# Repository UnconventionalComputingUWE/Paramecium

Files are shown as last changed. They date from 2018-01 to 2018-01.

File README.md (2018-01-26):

# Paramecium
Contained in this github are files to create and test artificial cilia.

%%%% Board manufacture %%%%
The eagle files are included in the github so that users may produce articifial cilia. There is a free version of EagleCAD for all users which allows for the modification and design of 2 layered boards, so anyone can edit the files. Some board manufacturers accept EagleCad files however some companies only accept Gerber files; there is a simple method of converting EagleCAD designs to Gerbers in the software.

%%%% Assembling the boards %%%%
The parts can be assembled on the boards by the user or by the board manufacturer should they have such capabilities. Some components are through-hole and some are surface-mount; both can be soldered by hand by anyone with reasonable soldering proficiency.

%%%% Uploading files to the board %%%%
You must upload the hex files (both the supplied one, and user created ones) using an ISP.
We used AVRDUDE to upload hex files via a USBtinyISP AVR Programmer Kit (USB SpokePOV Dongle) - v2.0. Other ISP devices may work.

Anyone is free to use and modify these designs and code for their use. Please provide appropriate credit, such as citations. Commercial use is permitted.

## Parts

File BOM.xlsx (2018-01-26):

 | Bill of Material
Part Name | Part | Mfr. Part. No | number (per board)
COLORSENS (Connectors) | HARWIN M20 Series Crimp Contact, Female, 30AWG to 22AWG, Gold, Tin Plating | M20-1180042 | 4
COLORSENS (Housing) | HARWIN M20-10, 2.54mm Pitch, 4 Way, 1 Row Female Straight Connector Housing | M20-1060400 | 1
U1 (socket) | 3M 4800 2.54mm Pitch Straight 28 Way, Through Hole Stamped pin Open Frame IC Dip Socket, 1A | 4828-3004-CP | 1
U1 | Microchip Technology ATMEGA328P-PU, 8bit AVR Microcontroller, 20MHz, 32 kB Flash, 28-Pin PDIP | ATMEGA328P-PU | 1
ISP | HARWIN M20, 2.54mm Pitch, 6 Way, 2 Row Unshrouded, Straight Pin Header, Through Hole, Solder Termination | M20-9980346 | 1
J1 | RS Pro 2.5mm PCB Mount DC Power Socket 1A | 448-376 | 1
 | Hex Socket Button Steel Black, Self-Colour Socket Screw, M3 x 5mm | Q107380000300005000 | 3
 | HTSB-M3-15-5-1, 15mm High Brass Threaded Hex Spacer 5mm Wide for M3 Thread | HTSB-M3-15-5-1 | 3
C3,C4 | KEMET 22pF Multilayer Ceramic Capacitor MLCC 50V dc ±5% C0G Dielectric 1206 (3216M), Max. Temp. +125°C | C1206C220J5GACTU | 2
 | HTSN-M3-20-6-2, 20mm High Nylon Threaded Hex Spacer 6mm Wide with 8mm Bolt Length for M3 Thread | HTSN-M3-20-6-2 | 3 (optional)
IC2 | Taiwan Semiconductor TS2937CP33 ROG, LDO Regulator, 500mA, 3.3 V, ±2%, -18 → 26 Vin 3-Pin DPAK | TS2937CP33 ROG | 1
Q2 | Crystal 16MHz, ±20ppm, 2-Pin HC-49/U-S SMD | QCS16.0000F18B23M | 1
C1,C2,C5,C6 | Nichicon Aluminium Electrolytic Capacitor 47μF 25V dc 6.3mm Surface Mount CD Series +105°C | UCD1E470MCL1GS | 4
IC1 | ON Semiconductor MC78M05CDTG Linear Voltage Regulator, 700mA, 5 V 3-Pin, D-PAK | MC78M05CDTG | 1
SV1,SV2,SV3,SV4 (Board connector, male) | HARWIN M20, 2.54mm Pitch, 5 Way, 1 Row Unshrouded, Straight Pin Header, Through Hole, Solder Termination | M20-9990546 | 3
S1 | 1 Way Surface Mount DIP Switch SPST, Raised Actuator Slide Actuator | IKD0103101 | 1
SV1,SV2,SV3 (Servo) | Tower Pro SG-50 Micro Digital Servo | SG50 | 3
COLORSENS | Adafruit RGB Sensor | TCS34725 | 1

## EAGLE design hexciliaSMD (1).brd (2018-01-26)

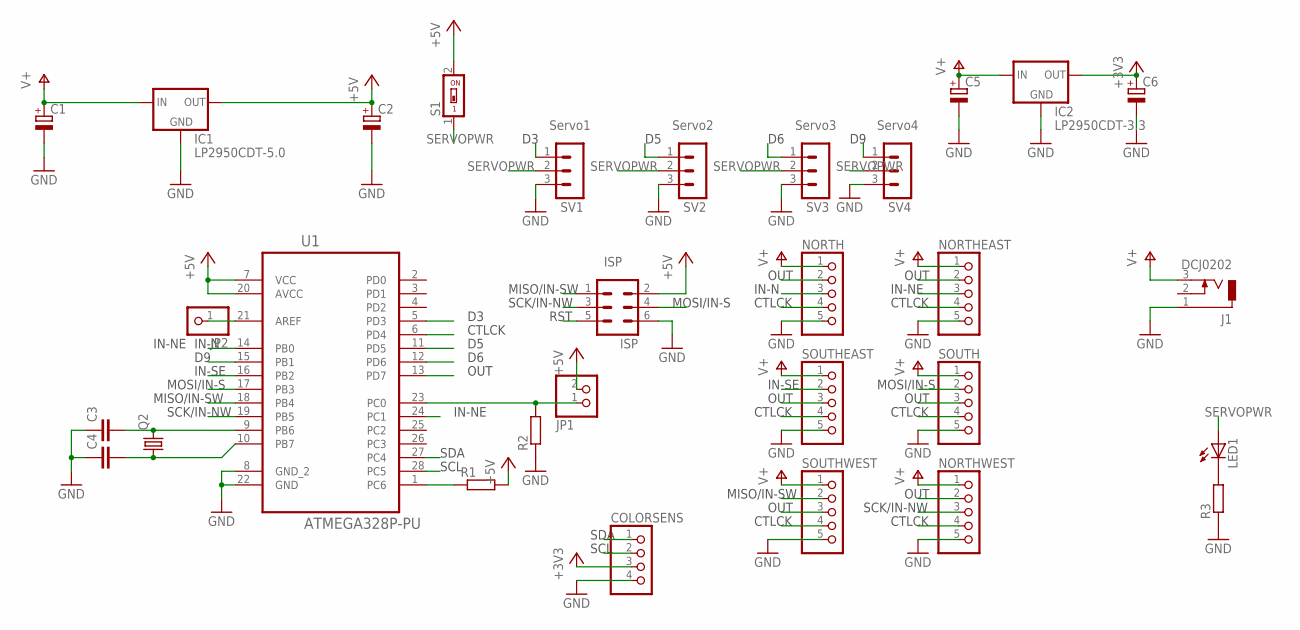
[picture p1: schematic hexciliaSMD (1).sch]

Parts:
C1, C2, C5, C6: CPOL-EU153CLV-0605; 153CLV-0605
C3, C4: C-EUC1210; C1210
COLORSENS: PINHD-1X4; 1X04
IC1: LP2950CDT-5.0; DPACK
IC2: LP2950CDT-3.3; DPACK
ISP: MA03-2
J1: DCJ0202
JP1: PINHD-1X2; 1X02
JP2: PINHD-1X1; 1X01
LED1: LEDCHIP-LED0805; CHIP-LED0805
NORTH: PINHD-1X5; 1X05
NORTHEAST: PINHD-1X5; 1X05
NORTHWEST: PINHD-1X5; 1X05
Q2: CRYSTALHC49UP; HC49UP
R1, R2, R3: R-EU_M1206; M1206
S1: SWS001; SMS-001
SOUTH: PINHD-1X5; 1X05
SOUTHEAST: PINHD-1X5; 1X05
SOUTHWEST: PINHD-1X5; 1X05
SV1, SV2, SV3, SV4: MA03-1
U1: ATMEGA328P-PU; DIP254P762X457-28

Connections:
+3V3: C6.+, COLORSENS.3, IC2.3 (OUT)
+5V: C2.+, IC1.3 (OUT), ISP.2, JP1.2, R1.2, S1.2, U1.7 (VCC), U1.20 (AVCC)
CONTROLCK: NORTH.4, NORTHEAST.4, NORTHWEST.4, SOUTH.4, SOUTHEAST.4, SOUTHWEST.4, U1.6 (PD4)
CTLCHK: JP1.1, R2.2, U1.23 (PC0)
D3: SV1.1, U1.5 (PD3)
D5: SV2.1, U1.11 (PD5)
D6: SV3.1, U1.12 (PD6)
D9: SV4.1, U1.15 (PB1)
GND: C1.-, C2.-, C3.1, C4.1, C5.-, C6.-, COLORSENS.4, IC1.4 (GND), IC2.4 (GND), ISP.6, J1.1, NORTH.5, NORTHEAST.5, NORTHWEST.5, R2.1, R3.1, SOUTH.5, SOUTHEAST.5, SOUTHWEST.5, SV1.3, SV2.3, SV3.3, SV4.3, U1.8 (GND_2), U1.22 (GND)
IN-N: NORTH.3, U1.14 (PB0)
IN-NE: NORTHEAST.3, U1.24 (PC1)
IN-SE: SOUTHEAST.2, U1.16 (PB2)
MISO/IN-SW: ISP.1, SOUTHWEST.2, U1.18 (PB4)
MOSI/IN-S: ISP.4, SOUTH.2, U1.17 (PB3)
unnamed: JP2.1, U1.21 (AREF)
unnamed: LED1.C, R3.2
unnamed: C3.2, Q2.2, U1.9 (PB6)
unnamed: C4.2, Q2.1, U1.10 (PB7)
OUT: NORTH.2, NORTHEAST.2, NORTHWEST.2, SOUTH.3, SOUTHEAST.3, SOUTHWEST.3, U1.13 (PD7)
RST: ISP.5, R1.1, U1.1 (PC6)
SCK/IN-NW: ISP.3, NORTHWEST.3, U1.19 (PB5)
SCL: COLORSENS.2, U1.28 (PC5)
SDA: COLORSENS.1, U1.27 (PC4)
SWPWR: LED1.A, S1.1, SV1.2, SV2.2, SV3.2, SV4.2
V+: C1.+, C5.+, IC1.1 (IN), IC2.1 (IN), J1.3, NORTH.1, NORTHEAST.1, NORTHWEST.1, SOUTH.1, SOUTHEAST.1, SOUTHWEST.1

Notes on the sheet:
Servo1
Servo2
Servo3
ISP
CTLCK
OUT
SDA
SCL
IN-N
IN-NE
IN-SE
MOSI/IN-S
MISO/IN-SW
SCK/IN-NW
RST
Servo4
SERVOPWR

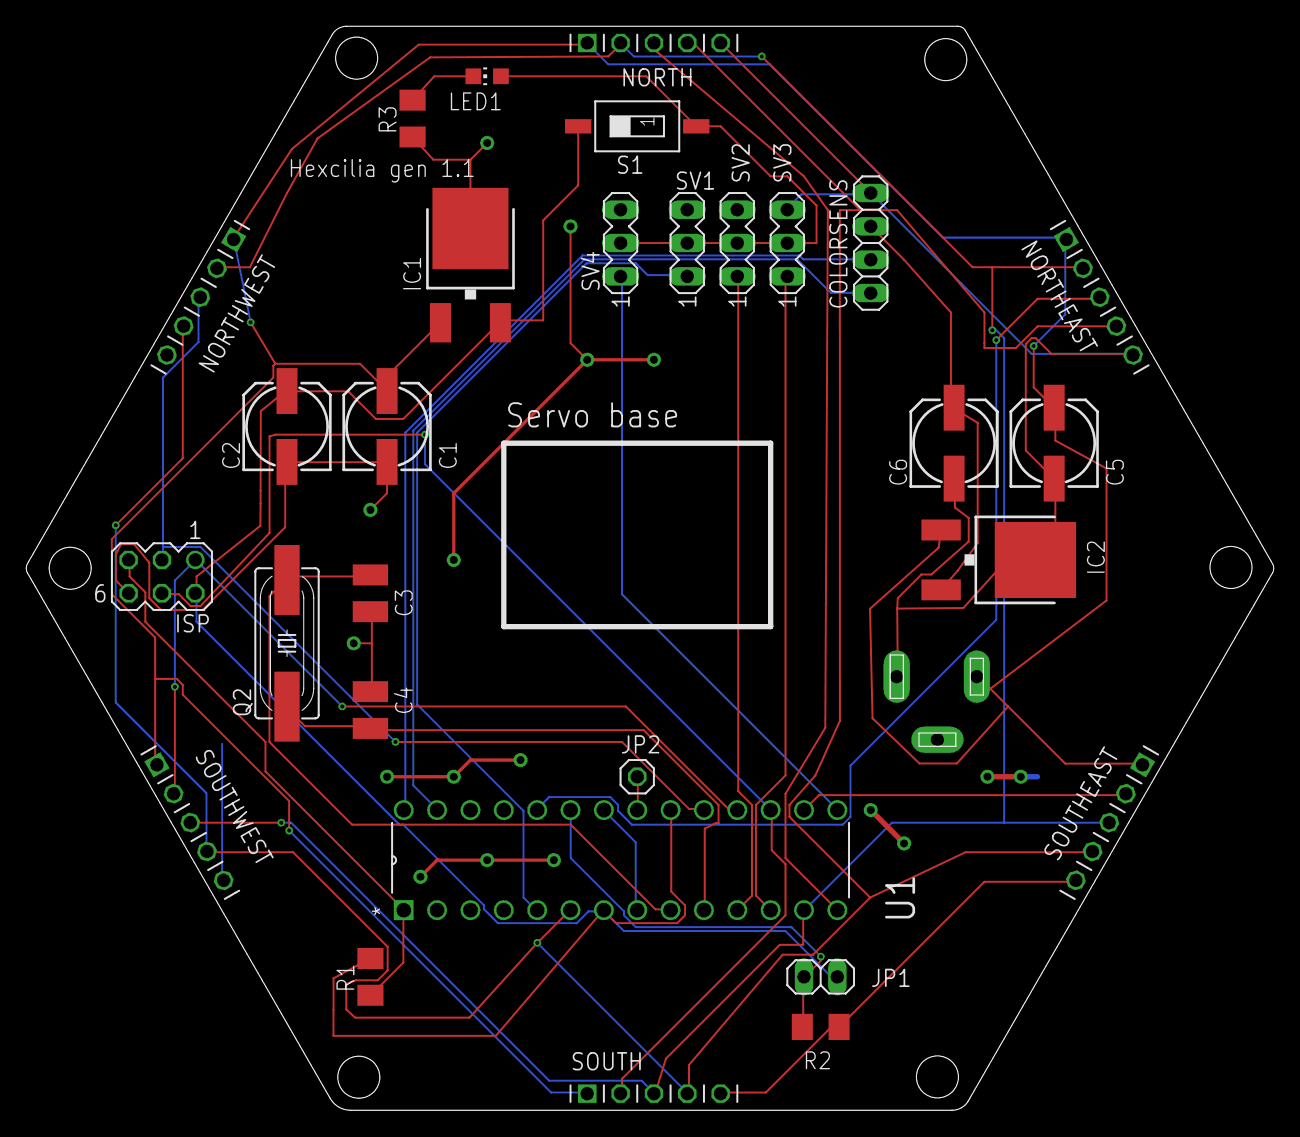
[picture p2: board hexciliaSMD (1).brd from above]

Board: 4 copper layers, 95.0 x 82.5 mm, 30 parts (1 on the bottom side), 25 nets.

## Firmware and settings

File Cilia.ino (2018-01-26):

// Working colour turning sketch with hexcilia. no local comms
#include <Wire.h>
#include <Servo.h>
#include "Adafruit_TCS34725.h"
//
Servo servo1;  // create servo object to control a servo
Servo servo2;
Servo servo3;
Servo servo4;
byte gammatable[256];
int val;
int digitalout=13;
int inN=8;
int inSE=16;
int inS=17;
int inSW=18;
int inNW=19;
int masterjumper=A0;
int inNE=A1;

#define redpin 3
#define greenpin 5
#define bluepin 6
// for a common anode LED, connect the common pin to +5V
// for common cathode, connect the common to ground
// set to false if using a common cathode LED
#define commonAnode true

Adafruit_TCS34725 tcs = Adafruit_TCS34725(TCS34725_INTEGRATIONTIME_50MS, TCS34725_GAIN_4X);
/////////////////////////////

void setup() {


  
  Serial.begin(9600);
  Serial.println("Color View Test!");
  if (tcs.begin()) {
    Serial.println("Found sensor");
  } else {
    Serial.println("No TCS34725 found ... check your connections");
    while (1); // halt!
  }
  
  for (int i=0; i<256; i++) {
    float x = i;
    x /= 255;
    x = pow(x, 2.5);
    x *= 255;
      
    if (commonAnode) {
      gammatable[i] = 255 - x;
    } else {
      gammatable[i] = x;      
    }
  }
}

void loop() {

  //startup position
    servo1.attach(3);
    servo2.attach(5); 
    servo3.attach(6);
    delay(50);
    
    servo1.write(0);            // tip return
    delay(100);    
    servo2.write(90);           // middle return
    delay(100);
    servo3.write(90);
    delay(100);
    servo1.detach();
    servo2.detach();
    servo3.detach();
    delay(50);    
     
     
     
  uint16_t clear, red, green, blue;
  tcs.setInterrupt(false);      // turn on LED
  delay(50);  // takes 50ms to read 
  tcs.getRawData(&red, &green, &blue, &clear);
  tcs.setInterrupt(true);  // turn off LED
      

if (clear > 1500){
  servo1.attach(3);
  servo2.attach(5); 
  servo3.attach(6);
 // servo4.attach(9);
      Serial.print("colour detected!  ");
      // Figure out some basic hex code for visualization
      uint32_t sum = clear;
      float r, g, b;
      r = red; r /= sum;
      g = green; g /= sum;
      b = blue; b /= sum;
      r *= 256; g *= 256; b *= 256;
      Serial.print("\t");
      if (r>g && r>b){ Serial.print("\tmostly red\t");
        val = 30;}
      if (g>r && g>b){ Serial.print("\tmostly green\t");
        val = 90;}
      if (b>r && b>g){ Serial.print("\tmostly blue\t");
        val = 170;}  
     Serial.println();
     
 ////// 
    // val = analogRead(potpin);            // reads the value of the potentiometer (value between 0 and 1023)
    // val = map(val, 0, 1023, 0, 180);     // scale it to use it with the servo (value between 0 and 180)
     servo3.write(val);                  // sets the servo position according to the scaled value
     delay(100); 
     Serial.println(val);
     Serial.println("sensor value");
     delay(50);  
     
     
     
     servo1.write(160);            // tip bending
     delay(200);    
     //Serial.println("power stroke");
     servo2.write(150);           // middle stroke
     delay(200);                       
     //Serial.println("tip beinding");
     servo1.write(0);            // tip return
     delay(100);    
     //Serial.println("return stroke");  
     servo2.write(90);           // middle return
     delay(100);   
     //Serial.println("tip return");
  servo1.detach();
  servo2.detach(); 
  servo3.detach();
  delay(50);
  }
}
